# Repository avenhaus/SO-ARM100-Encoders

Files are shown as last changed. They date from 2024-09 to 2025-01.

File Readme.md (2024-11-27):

# <center>Magnetic Encoder Dummy Servo</center>

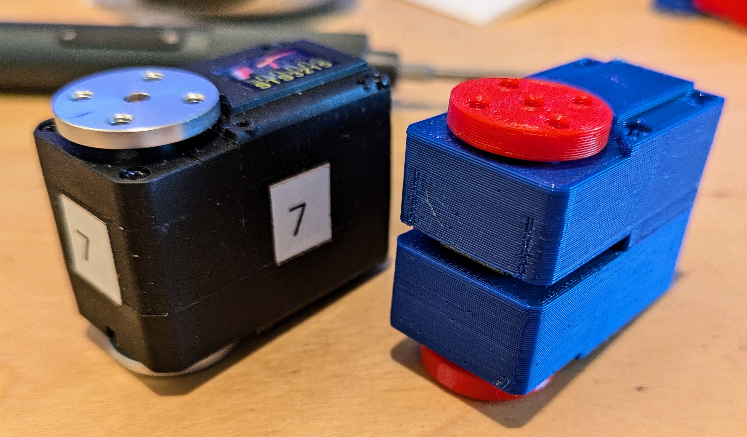
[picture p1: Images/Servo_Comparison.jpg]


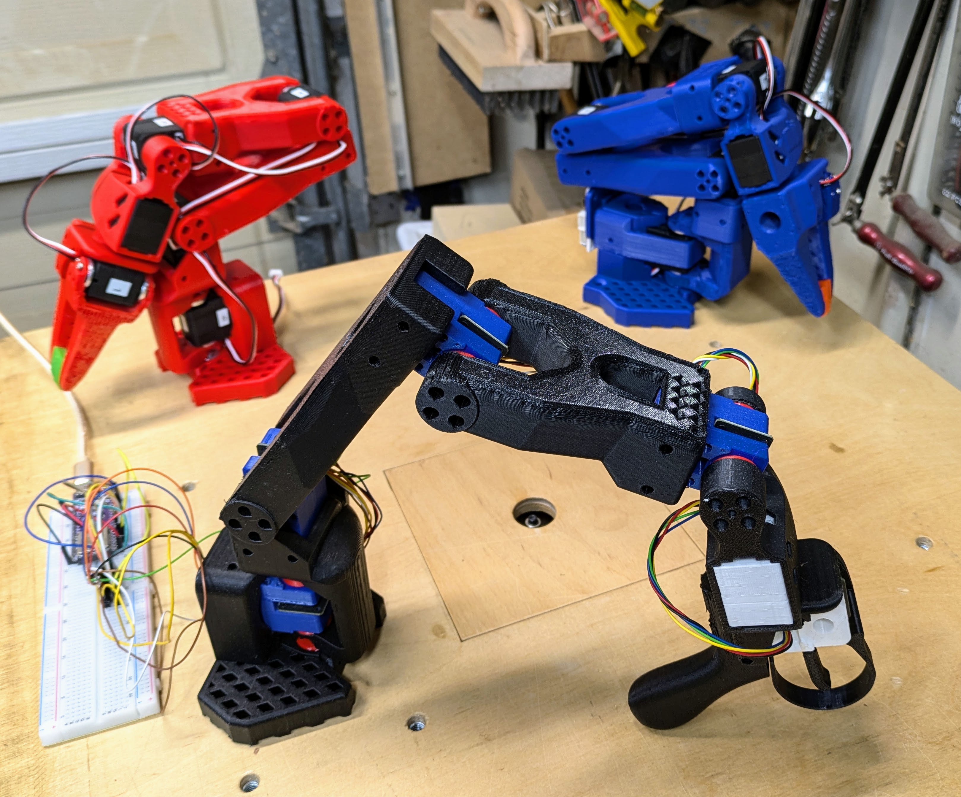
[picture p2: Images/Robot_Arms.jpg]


## Summary
This project is related to 
https://github.com/huggingface/lerobot
and
https://github.com/TheRobotStudio/SO-ARM100

It explores to use much cheaper magnetic encoders for the Leader Arm instead of the regular servos. These dummy servos are also much easier to move manually, as there is no gear train that needs to back drive the servo motor. This makes them ideal for the Leader Arm.

## Custom PCB

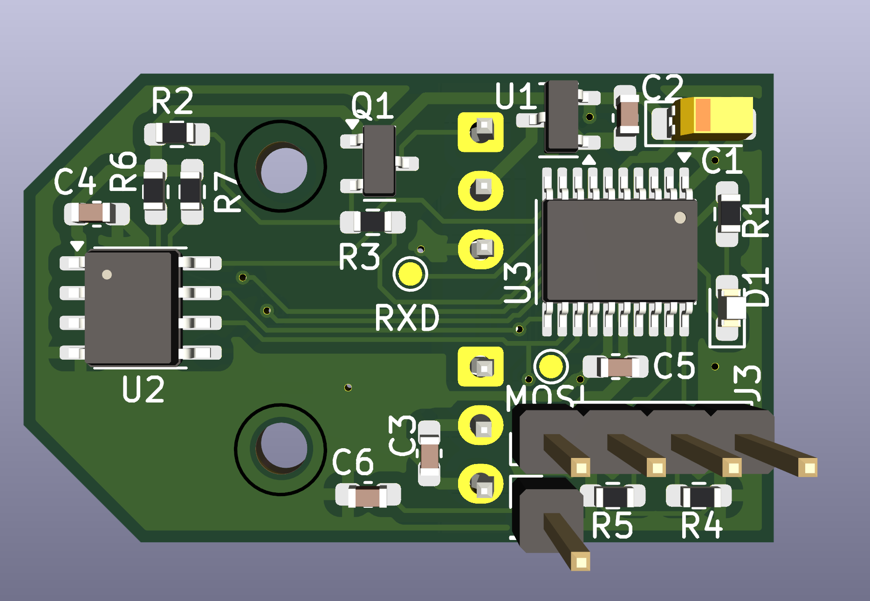
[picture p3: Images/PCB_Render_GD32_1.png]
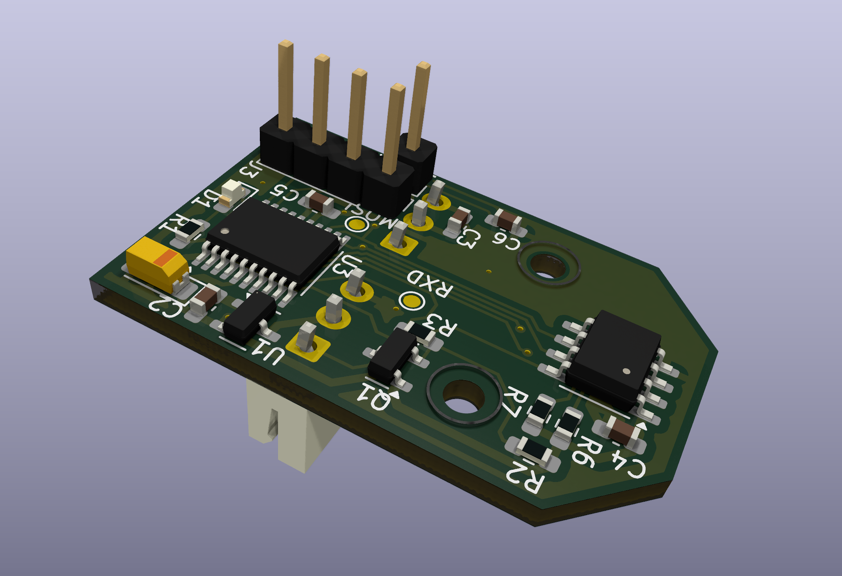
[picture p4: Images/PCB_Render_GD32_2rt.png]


The custom PCB makes it possible to daisy chain magnetic encoders for much easier wiring. The PCB uses a microcontroller that emulates a FeeTech servo. The dummy servos can be connected to the same servo controller board and no special software is needed.

### Manufacturing
TODO: JLCPCB

### Cables and Connectors

FeeTech servos use 3-pin 5264 connectors. However, JST XH connectors are more common and pre-made cables are much easier to find. The PCB can be populated with either of the connector types. If JST connectors are used, an adapter needs to be made to connect to the 5264 connector on the controller board. Alternatively one can simply cut off one end from a pre-made cable and solder it directly to the controller board.

The dummy servos use very little current. So any gauge wire should be ok. However, if they are to be mixed with real servos on the same bus, wire gauge needs to be taken into consideration.

The servos use "reverse double head" cables (pin 1 connected to pin 1, etc.) although in a pinch it's also possible to switch the terminals on "same side' cables yourself.

JST XH: https://www.aliexpress.us/w/wholesale-JST-XH-3.html
JST XH cables: https://www.aliexpress.us/w/wholesale-xh-double-head.html

5264: https://www.aliexpress.us/w/wholesale-5264.html
5264 cables: https://www.aliexpress.us/w/wholesale-5264-double-head.html https://www.aliexpress.us/item/3256806128255434.html

### Magnets

Normally magnetic encoders use special, radially magnetized magnets.

Magnets https://www.aliexpress.us/w/wholesale-encoder-magnets.htm

However, it is also possible to use the regular, axially magnetized 6x3 disk magnets which are cheaper. They just have to be oriented sideways. Print the corresponding servo horn instead. N35 magnets are fine. Nothing fancy is needed.

https://www.amazon.com/s?k=6x3mm+magnet
https://www.aliexpress.us/w/wholesale-6x3-magnet.html

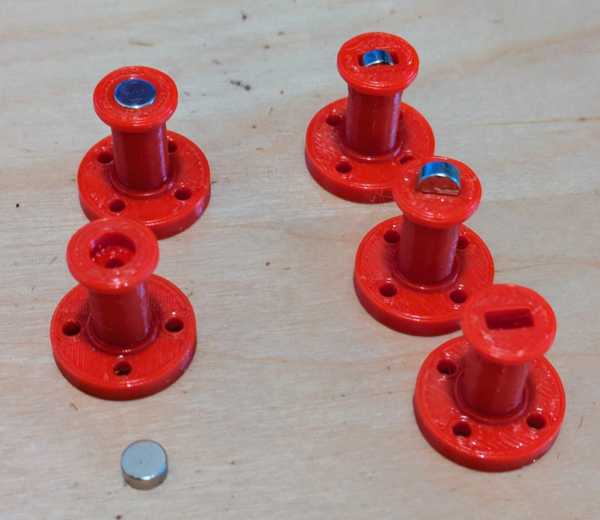
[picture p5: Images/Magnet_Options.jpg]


### Firmware Programming

See: [Firmware](Firmware)

### 3D Printed Servo Housing

<p align="center">
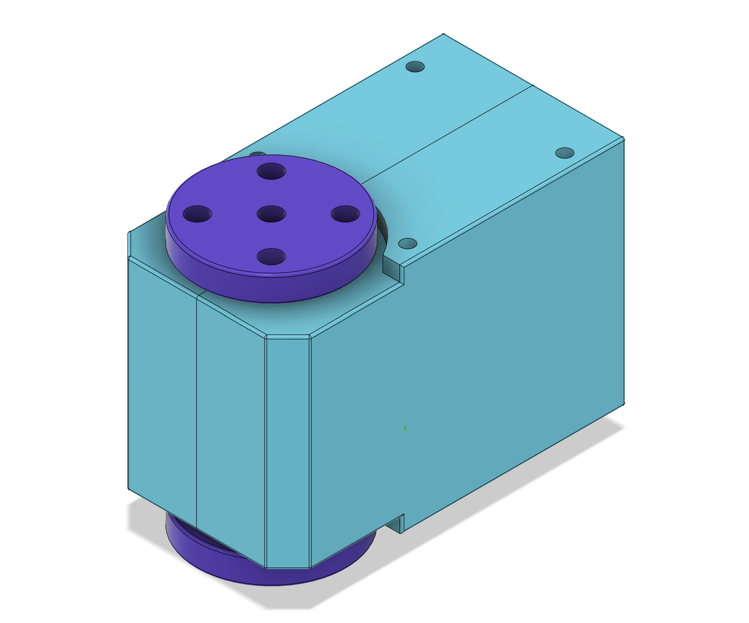
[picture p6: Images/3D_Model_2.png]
 
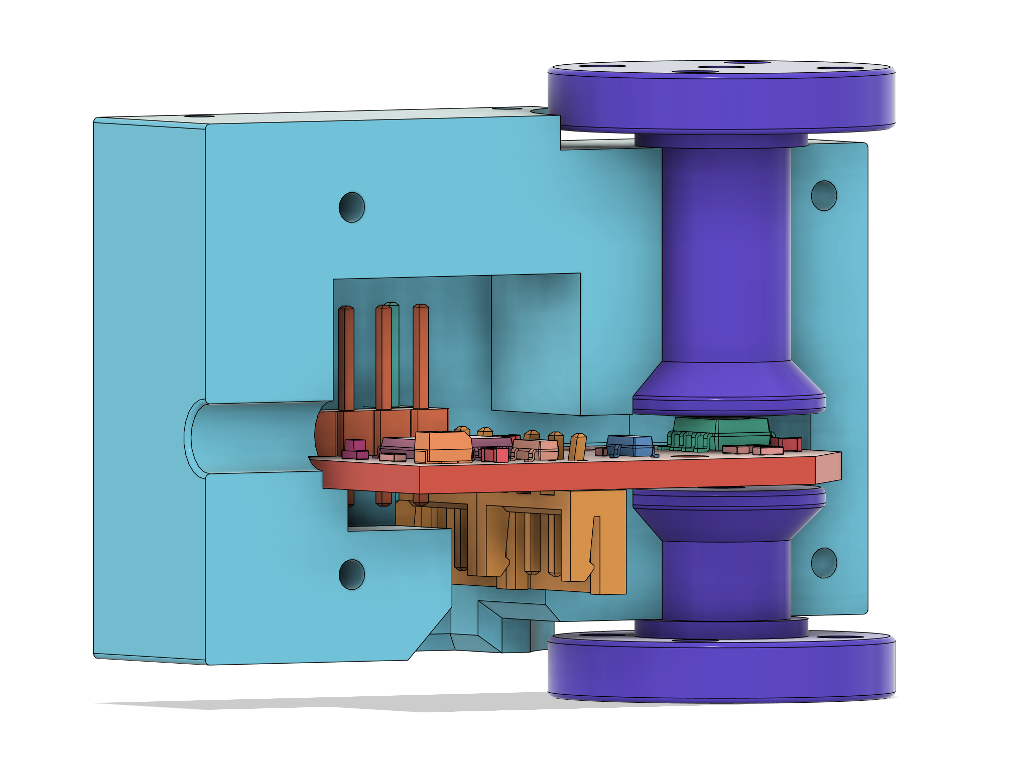
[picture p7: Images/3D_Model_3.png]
</p>
<p align="center">
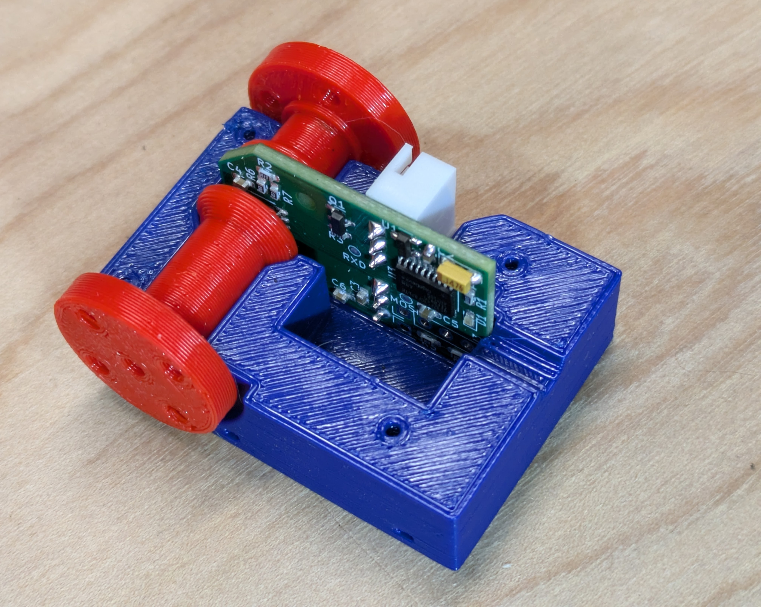
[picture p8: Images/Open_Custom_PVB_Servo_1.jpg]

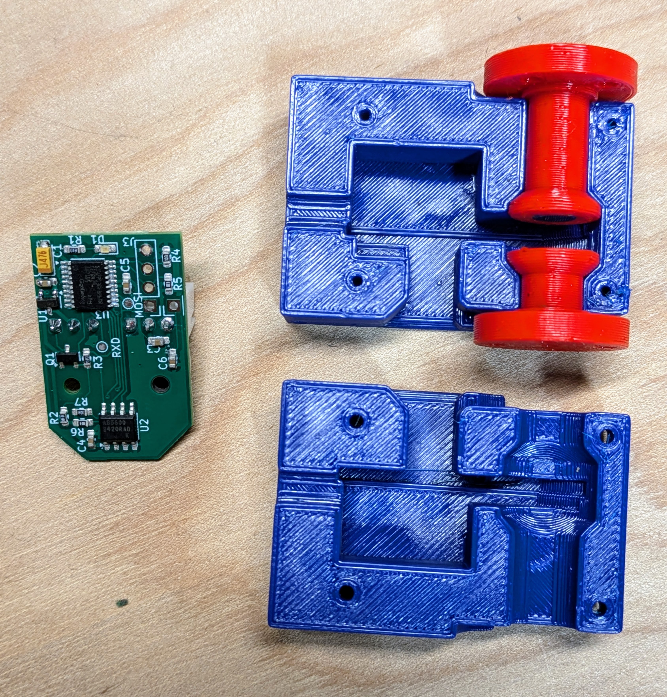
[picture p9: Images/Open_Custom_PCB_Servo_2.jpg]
</p>

## Off the Shelve Hardware

Instead of using a custom PCB it is also possible to use off the shelve parts. This requires more hand wiring.

### Magnetic Rotary Encoders
Currently there are two cheap and popular magnetic encoders on AliExpress, the AS5600 and the MT6701.
The AS5600 is older, has 12 bit resolution (4096) and supports only I2C. Since the chip has only one hard coded ID, that makes it hard to use when multiple of them are needed.
The MT6701 has 14 bit resolution (16,383) and also supports a SSI interface, which is similar to SPI.

AliExpress offers several MT6701 breakout boards some of which can be purchased in low quantities for less than $2 including magnet.

[AliExp MT6701](https://www.aliexpress.com/w/wholesale-MT6701.html)

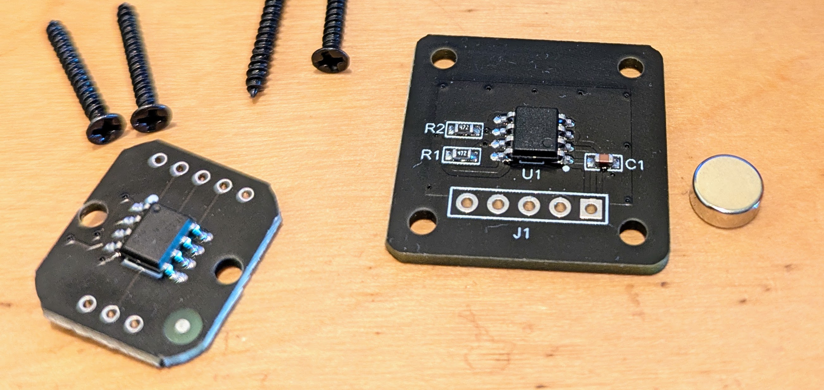
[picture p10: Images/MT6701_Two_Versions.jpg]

<p>






The larger version only has the I2C pins on the header and must be modified to work with SSI. The trace to the middle pin of the header needs to be cut and IC pin 8 lifted and connected to that header pin instead. It is also slightly too large, sticking out a bit in front of the servo. It can be made to work, but the smaller board is much easier to use and therefor recommended. However the smaller board does not come with magnets. They must be purchased separately. Only radially magnetized magnets can be used. Normally disk magnets are magnetized axially. 

[AliExp Radial Magnets](https://www.aliexpress.us/item/3256804628068823.html)

### 3D Printed Servo Housing

There are two slightly different versions of the housing. The simple version does not retain the servo horns by itself. It relies on the structure of the robot arm to keep them in place. This version is slightly simpler and is used for the lower 4 arm servos.

The wrist and gripper need the horn to be held in place by the servo itself. For these joints the top is split into two parts and the horn axle is not just a straight cylinder.

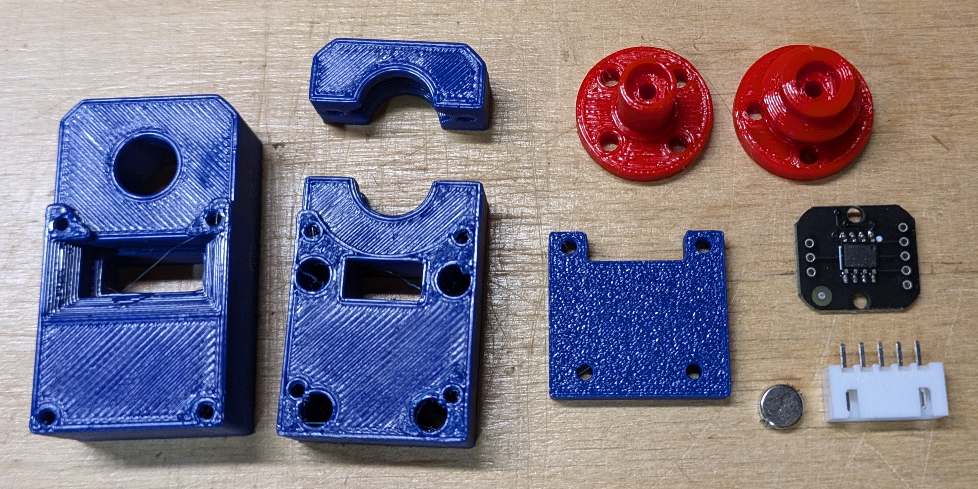
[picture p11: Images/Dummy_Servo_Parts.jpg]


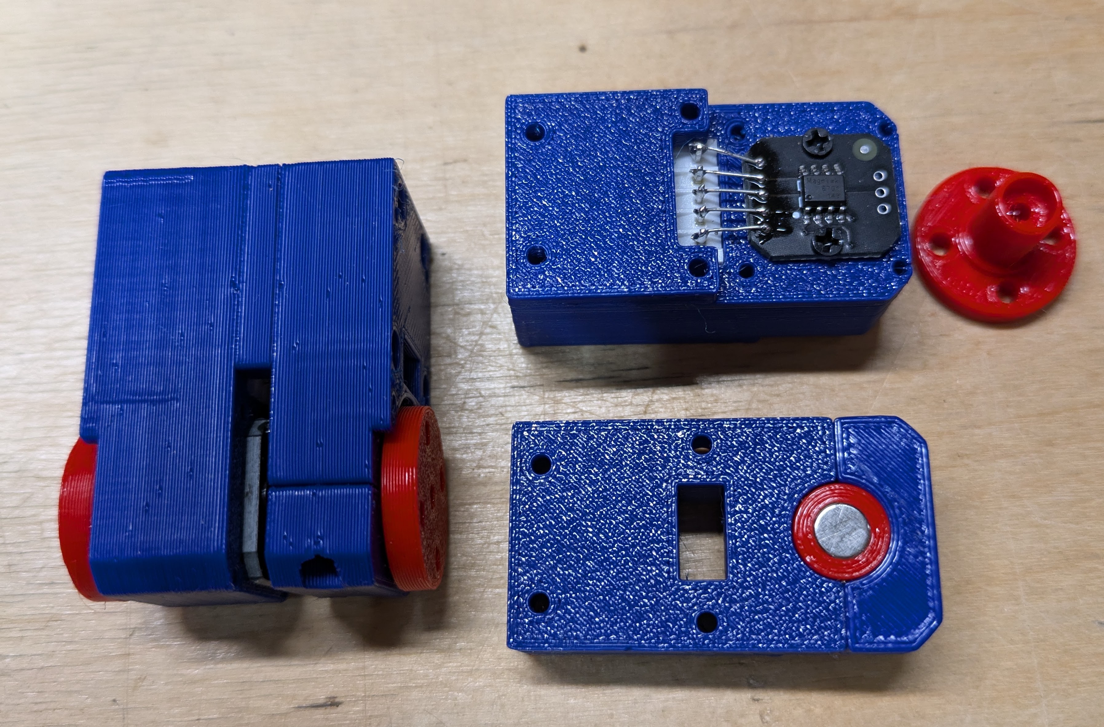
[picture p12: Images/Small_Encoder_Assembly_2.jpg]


**Big Board Alternative**

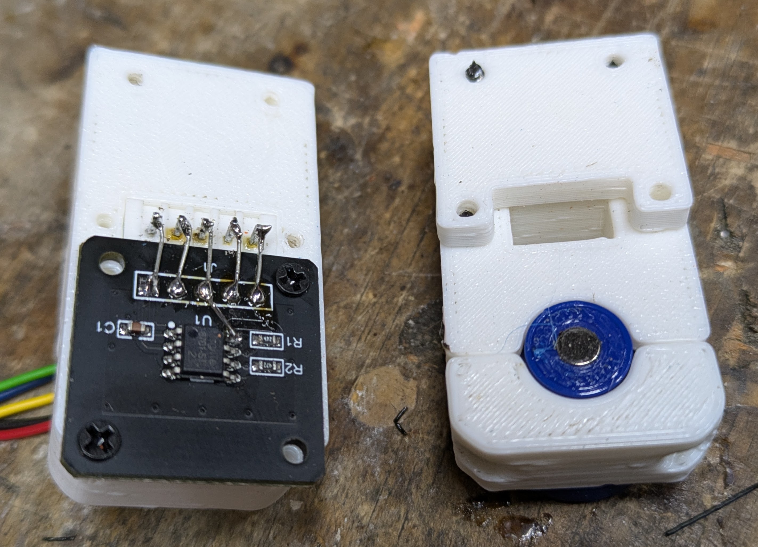
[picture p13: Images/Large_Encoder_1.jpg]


The [Dummy Servo](./Hardware) is 3D printed.
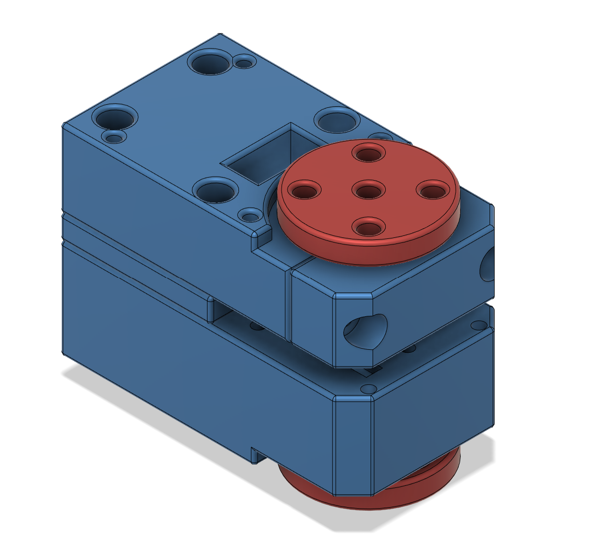
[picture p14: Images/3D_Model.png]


## Software

A simple [Arduino](./Arduino) / PlatformIO project is used to read the six encoders and send their values over a serial USB port to the PC.

On the PC side a small [Python](./Python) program receives the values from the serial port and uses the Feetech-SDK to control the servos of the follower arm.

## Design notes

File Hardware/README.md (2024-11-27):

# <center>3D Models</center>



## Custom PCB

The PCB can be populated with either an AS5600 or an MT6701 encoder. The MCU can automatically figure out which one is connected. However at the moment there are only non blocking drivers for the AS5600.

There are two versions of the PCB. One for the GD32F130 microcontroller, which is also used by Feetech servos. The other one uses a CH32V003 instead, which is cheaper. However no firmware has been written yet for the CH32V003 and the PCB has not been tested.

### Programming Dongles

The GD32F130 is programmed with a ST-LINK V2 dongle: https://www.aliexpress.us/item/3256805941217455.html / https://www.aliexpress.us/item/3256805308308820.html

The CH32V003  is programmed with a WCH-linkE dongle: https://www.aliexpress.us/item/3256804084637506.html

### Solder Stencil

[Cutting solder paste stencils from Mylar YouTube video](https://www.youtube.com/watch?v=mw0mskVCvis)
[make_stencil.py GitHub](https://github.com/bminch/Eclectronics)

- Open KicCAD PCB => Plot 
- Select layers: F. Paste and Edge Cuts
- Plot Format: SVG
- python make_stencil.py gd32_encoder

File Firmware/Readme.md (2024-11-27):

# <center>Magnetic Encoder Dummy Servo Firmware</center>

The firmware implements the Dynamixel protocol to emulate a FeeTech servo. It reads the magnetic encoder and also supports writing configurations to EEPROM.

The firmware is developed in Visual Studio Code with the PlatformIO extension. The firmware is based on the Arduino framework.

### Drivers

Arduino drivers are blocking. They contain busy loops that wait while the sensor is being read. The Dynamixel protocol which is used to control the FeeTech servos times out if there is no immediate response upon a communication request. For this reason custom, non blocking drivers for the I2C / SPI peripherals as well as the magnetic encoders have to be implemented.

## Programming

The GD32F130 is programmed with a ST-LINK V2 dongle: https://www.aliexpress.us/item/3256805941217455.html / https://www.aliexpress.us/item/3256805308308820.html

The CH32V003  is programmed with a WCH-linkE dongle: https://www.aliexpress.us/item/3256804084637506.html

The PCB has holes for a programming header, but that does not need to be populated. It is usually possible to just loosely insert the connectors and press them sideways with a finger while programming to make good enough contact.

**The programming header has a 3.3V pin. That 3.3V should only be connected if there is no voltage on the servo com headers!**

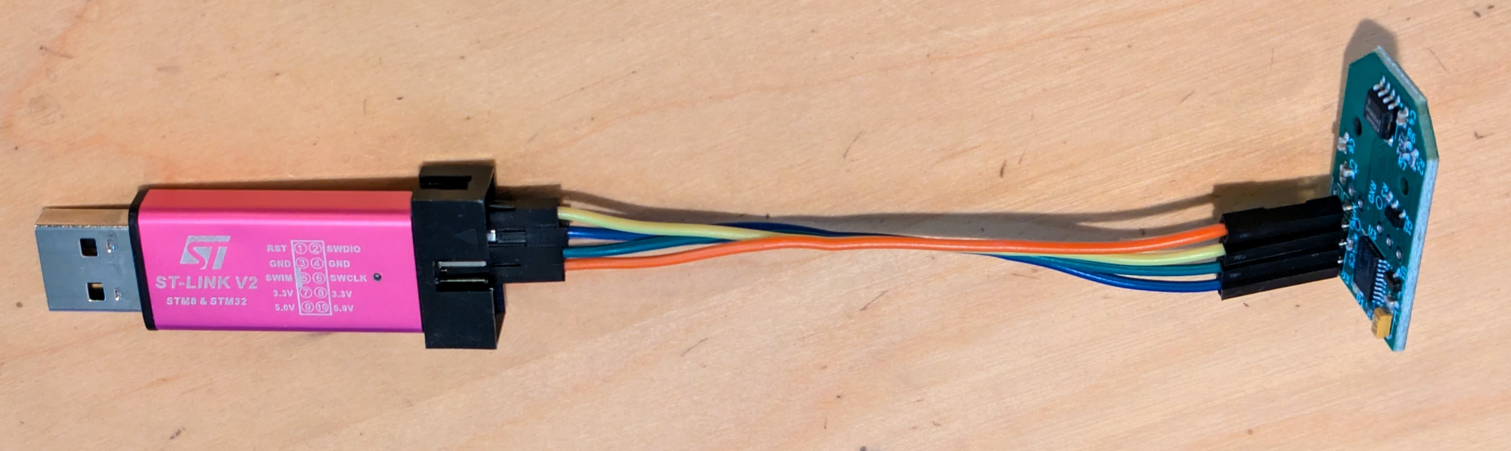
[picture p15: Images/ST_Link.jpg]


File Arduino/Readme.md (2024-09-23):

# Controller to read MT6701 magnetic encoders

PlatformIO / Arduino code to read six MT6701 magnetic encoders over SSI (SPI) and send the data to the UART serial port.

The MT6701 has a 14 bit resolution (0-16383).
To address six encoders, 10 wires are needed: VCC, GND, Clock, Data, 6 x CS.

https://www.lcsc.com/datasheet/lcsc_datasheet_2110291630_Magn-Tek-MT6701QT-STD_C2913974.pdf

## Output Format

The output are comma separated values. The first value is the timestamp in ms since the controller reset. This is followed by angle (float) and status (int) pairs for each encoder.

Lines that start with # are text status messages.

## Calibration

Move all arm joints to the home postion and press the button on the dev board.
This will save the current positions to EEPROM. 
All angles from now on will be sent as realtive to this position.

## Connections

* SPI_SCK_PIN 12
* SPI_MISO_PIN 13
* SPI_CS0_PIN 4
* SPI_CS1_PIN 5
* SPI_CS2_PIN 6
* SPI_CS3_PIN 7
* SPI_CS4_PIN 8
* SPI_CS5_PIN 9

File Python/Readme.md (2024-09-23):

# Simple Follower

Read the MT6701 magnetic encoders and send values to the Feetech STS3215 servos of a follower arm.

conda create -y -n encoder_arm python=3.10
conda activate encoder_arm
pip install feetech-servo-sdk

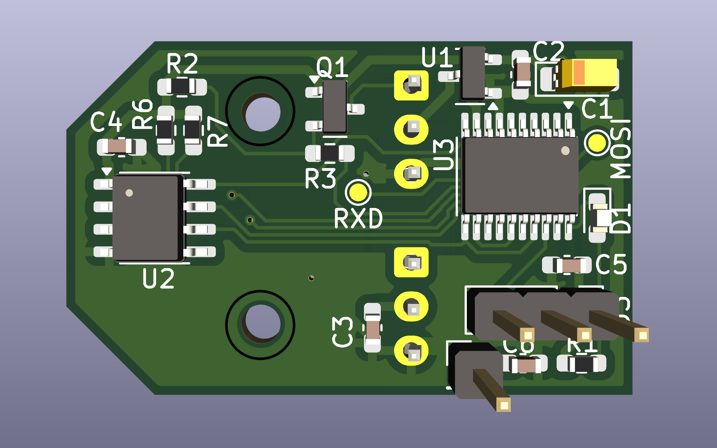
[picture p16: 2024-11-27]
Images/PCB_Render_CH32_1.png

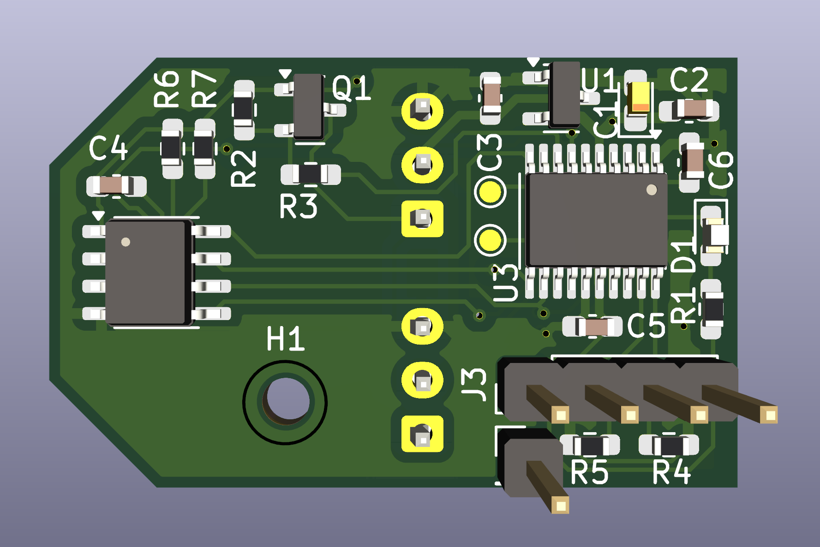
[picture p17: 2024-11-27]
Images/PCB_Render_1.png

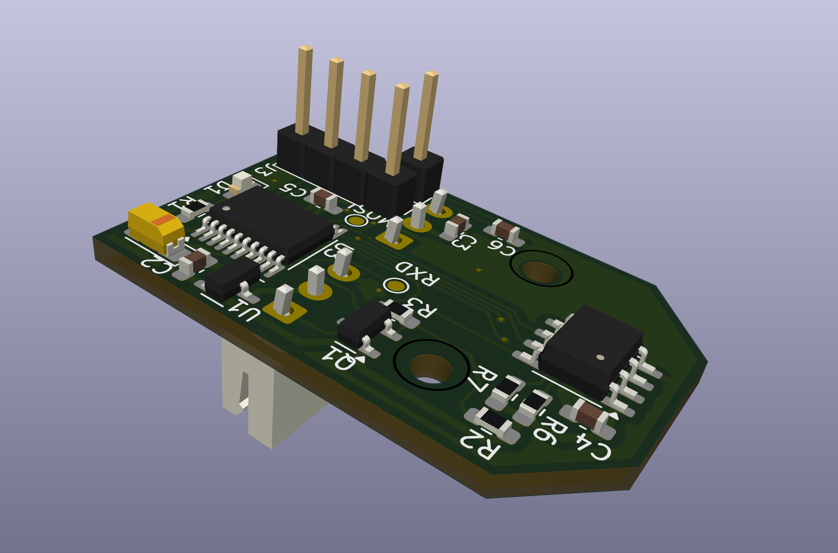
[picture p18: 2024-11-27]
Images/PCB_Render_GD32_2.png

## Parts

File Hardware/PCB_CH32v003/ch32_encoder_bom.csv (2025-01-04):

Id | Designator | Footprint | Quantity | Designation | Supplier and ref
1 | MOSI | TestPoint_Pad_D1.0mm | 1 | MOSI
2 | TP1 | PinHeader_1x01_P2.54mm_Vertical | 1 | RST
3 | C1 | CP_EIA-3216-18_Kemet-A_Pad1.58x1.35mm_HandSolder | 1 | 47uF
4 | C2,C5,C3,C6,C4 | C_0603_1608Metric_Pad1.08x0.95mm_HandSolder | 5 | 100nF
5 | R1 | R_0603_1608Metric_Pad0.98x0.95mm_HandSolder | 2 | 1K
6 | J3 | PinHeader_1x03_P2.54mm_Vertical | 1 | Conn_01x03_Pin
7 | U2 | SO-8_3.9x4.9mm_P1.27mm | 1 | AS5600 or MT6701CT
8 | R3 | R_0603_1608Metric_Pad0.98x0.95mm_HandSolder | 1 | 100
9 | R2,R7,R6 | R_0603_1608Metric_Pad0.98x0.95mm_HandSolder | 2 | 10K
10 | D1 | LED_0603_1608Metric_Pad1.05x0.95mm_HandSolder | 1 | LED
11 | U1 | SOT-23-3 | 1 | HT7533S
12 | RXD | TestPoint_Pad_D1.0mm | 1 | RXD
13 | Q1 | SOT-23 | 1 | 2N7002K
14 | U3 | TSSOP-20_4.4x6.5mm_P0.65mm | 1 | CH32V003FxPx
15 | J1,J2 | JST_1x03_P2.50mm_Vertical | 2 | Conn_01x03_Pin

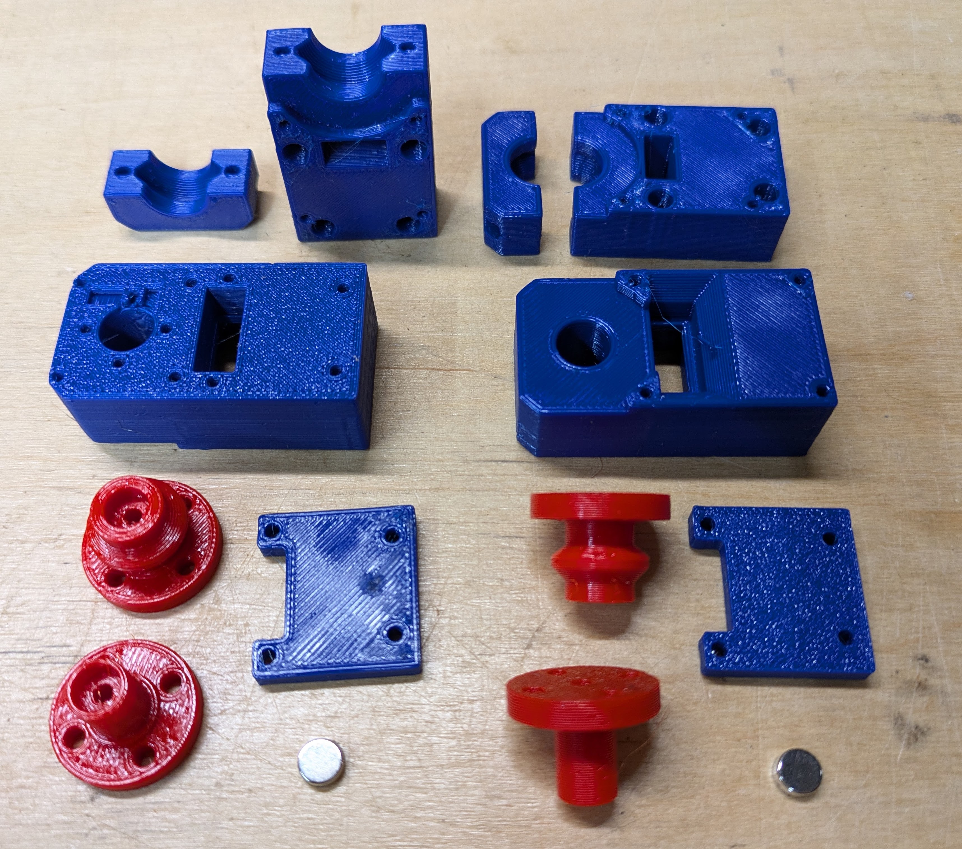
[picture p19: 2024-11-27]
Images/3D_Printed_Parts.jpg

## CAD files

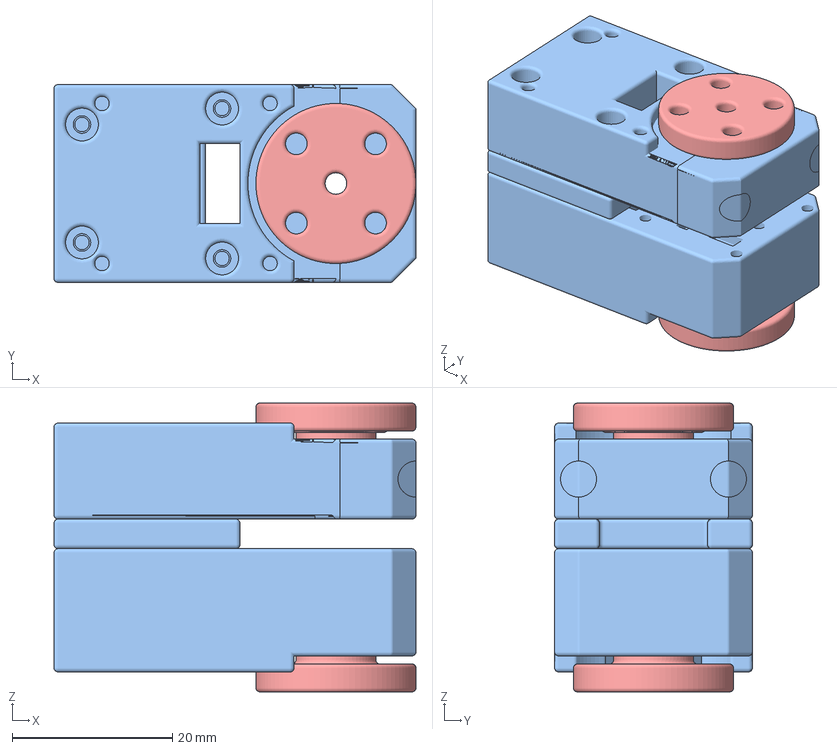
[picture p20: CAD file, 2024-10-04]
Hardware/3D_Models/Off the shelve PCB/Encoder Dummy Servo.3mf
45.2 x 24.7 x 36.1 mm
Clip
Horn x 3
Top

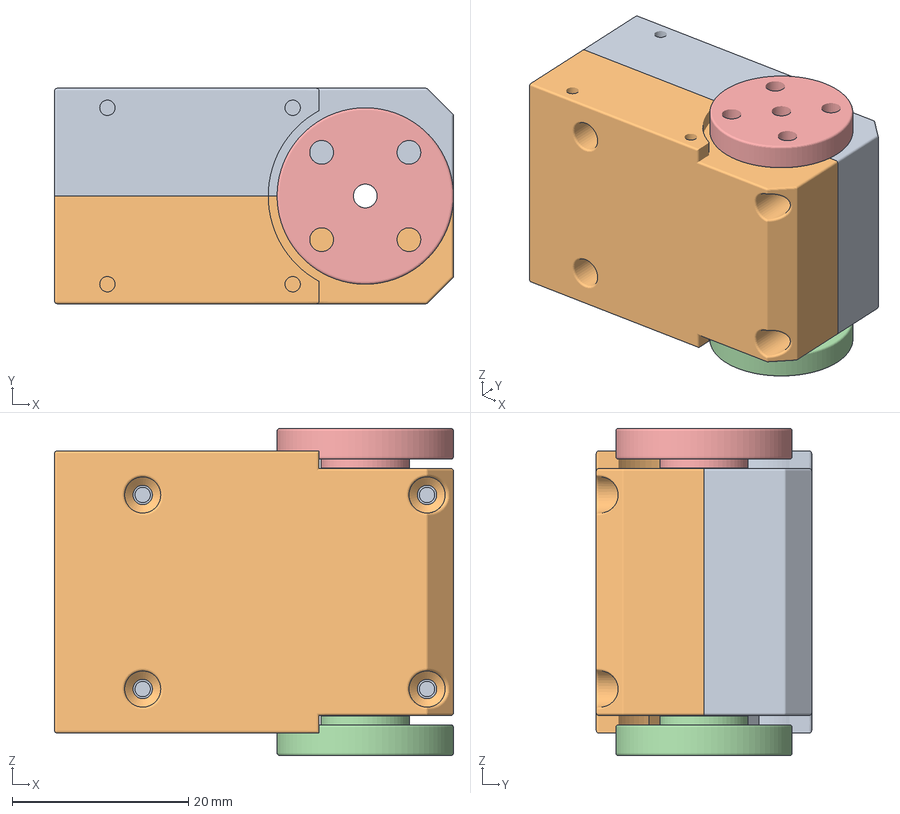
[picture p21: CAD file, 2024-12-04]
Hardware/3D_Models/Servo Custom PCB V2/Servo Custom PCB V2.3mf
45.2 x 24.4 x 37.1 mm
Back
Front
Horn Magnet 6x3
Idle Horn
Magnet Horn 5mm radial
Magnet Horn 6mm radial

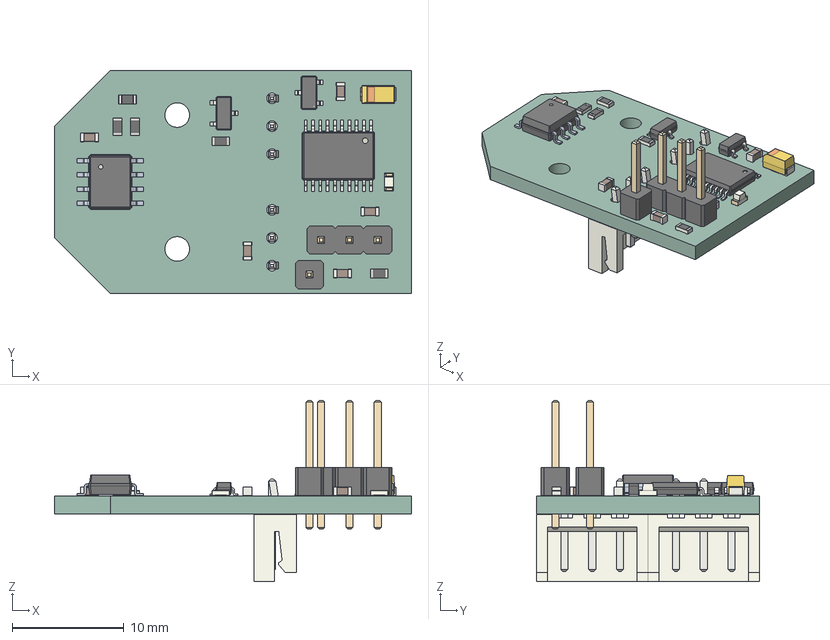
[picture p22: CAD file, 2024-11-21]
Hardware/PCB_CH32v003/ch32_encoder_v0.7.step
32.0 x 20.0 x 16.2 mm
PinHeader_1x01_P254mm_Vertical
CP_EIA_3216_18_Kemet_A
C_0603_1608Metric x 5
R_0603_1608Metric x 5
PinHeader_1x03_P254mm_Vertical
CQ assembly
LED_0603_1608Metric
SOT-23-3
SOT_23
TSSOP_20_44x65mm_P065mm
JST_B3B_EH_A x 2
ch32_encoder_PCB

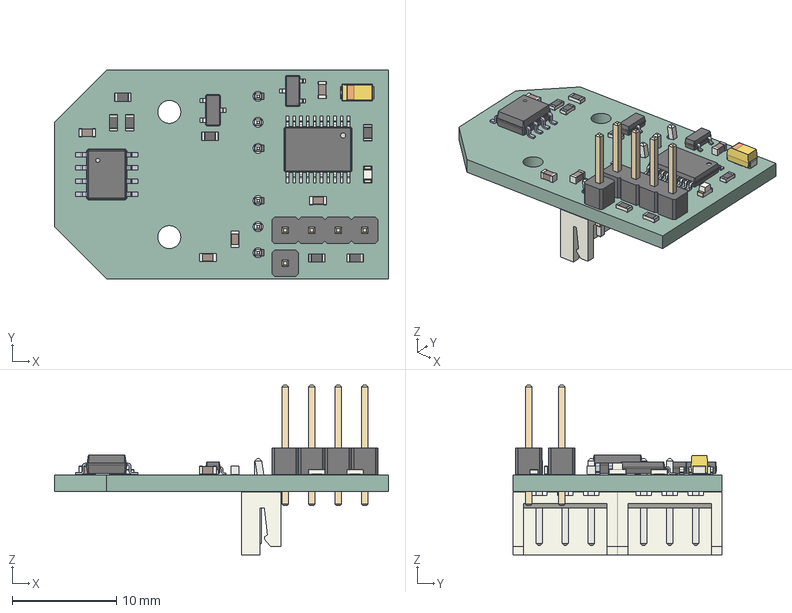
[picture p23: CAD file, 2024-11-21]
Hardware/PCB_GD32F130/gd32_encoder_v0.7.step
32.0 x 20.0 x 16.2 mm
R_0603_1608Metric x 7
PinHeader_1x01_P254mm_Vertical
CP_EIA_3216_18_Kemet_A
C_0603_1608Metric x 5
TSSOP_20_44x65mm_P065mm
CQ assembly
PinHeader_1x04_P254mm_Vertical
LED_0603_1608Metric
SOT-23-3
SOT_23
JST_B3B_EH_A x 2
gd32_encoder_PCB

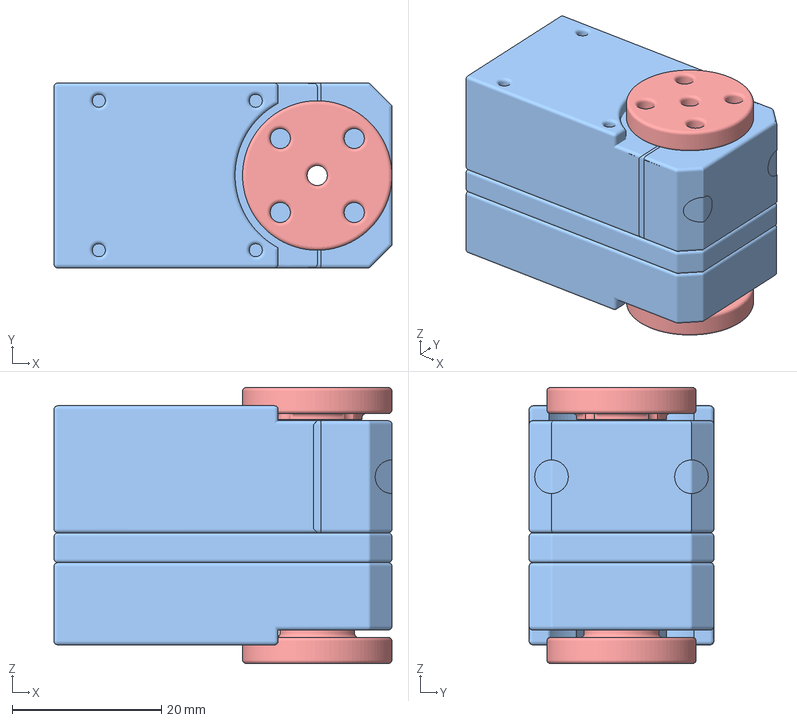
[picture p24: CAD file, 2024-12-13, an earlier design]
Hardware/3D_Models/Servo Custom PCB V1/Servo Custom PCB V1.3mf
45.2 x 24.7 x 37.0 mm
Clip
Horn x 3
Top

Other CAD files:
Hardware/3D_Models/Off the shelve PCB/Encoder Dummy Servo.f3d
Hardware/3D_Models/Servo Custom PCB V1/Servo Custom PCB V1.f3d
Hardware/3D_Models/Servo Custom PCB V2/Servo Custom PCB V2.f3d

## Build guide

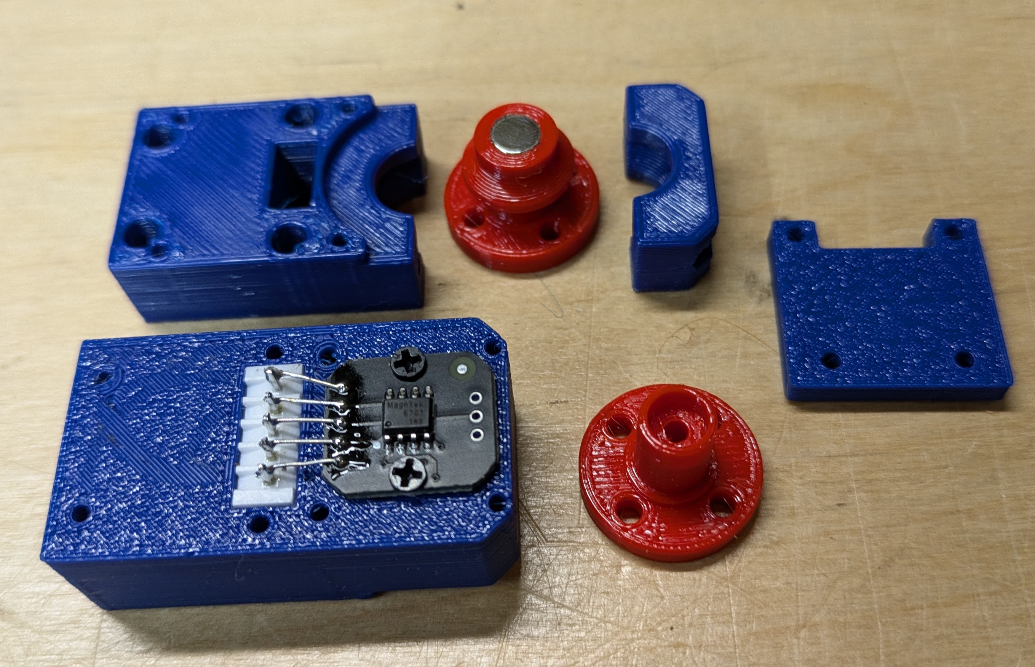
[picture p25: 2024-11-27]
Images/Small_Encoder_Assembly_1.jpg

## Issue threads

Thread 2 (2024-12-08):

Pre-assembled or Custom PCB: Which Do You Recommend?

seanwhen, 2024-12-08:
I’m not very experienced with PCB design, and in the past, my soldering attempts often resulted in damaged or burned boards. For the MT6701, do I need to purchase an ESP32 to use the pre-assembled board? I didn’t see this combination explicitly mentioned in the project’s BOM. From the images, it seems that the encoder is fixed onto a 3D-printed mount, with all the wires connected to a breadboard, which then interfaces with an ESP32/STM32. Is this understanding correct?

Additionally, in the video you shared earlier, the delay seemed comparable to the STS3215 servo. Among the three options—pre-assembled MT6701, custom PCB, and the STS3215 servo—how do they compare in terms of precision based on your experience? Do you see significant advantages in moving towards custom PCBs, or would you recommend sticking with the off-the-shelf solutions? Thank you for your insights!

avenhaus, 2024-12-11:
Hi Seanwen, the custom boards are SMD and probably not easy to assemble yourself if you don't already have experience. JLCPCB can assemble boards for you, but I have not tried this myself and don't know what it would cost.

For pre assembled boards yes, you will also need to buy an ESP32 board, which will drive the individual sensor boards and translate the data to serial data and connect to the PC. Delay should not be an issue and MT6701 actually have higher resolution than the STS3125.

However be aware that there is not the same software support on the PC side. I have a simple program to do remote control of another arm, but I have not looked into how to integrate this into the other SO-ARM100 software to do training etc. So there is still a driver portion missing.

seanwhen, 2024-12-12:
Hi, thank you for your detailed response! I’ve completed the custom PCB design and 3D enclosure based on your project and am about to assemble and test the PCB. From your explanation, it seems that the basic control program for the custom PCB works with “飞特.exe,” but integrating it seamlessly into LeRobot might pose some challenges. Is this correct?

Additionally, from my understanding, the custom PCB design already includes a chip on each board, so it does not require an ESP32, whereas the MT6701-based solution does require an ESP32. Is that correct? Based on this, I’d like to clarify the following points:
	1.	Using custom PCBs with LeRobot:
If I use the custom PCB (with a chip on each board), will I still need to write additional drivers to make it compatible with LeRobot?
Does LeRobot currently support extending to use custom PCBs directly, or would I need to modify its source code?
	2.	Future plans for control program updates:
Do you plan to update the control program to integrate custom PCB support into LeRobot?
Alternatively, could you share the protocol details or source code of the existing control program so I can build on it for further development and integration?

Thank you again for your amazing work, and I look forward to your reply!

avenhaus, 2024-12-13:
Oh wow, you are brave! Good luck with the assembly!

Yes, if you use the custom PCB, you do not need an ESP32. The idea is that the custom PCB will emulate an STS3215 and look the same to the software. Instead you will need the driver board from FeeTech or WaveShare to connect to the PC, same as servos.

1) In the end LeRobot should not be able to tell the difference between an STS3215 and these boards. So no custom drivers are needed. But [iamliustar](https://github.com/iamliustar) found a few things missing in the current firmware that need to be added. Please see https://github.com/avenhaus/SO-ARM100-Encoders/issues/1 for details.

2) No changes should be needed in LeRobot unless you use the ESP32 with of the shelve encoders. The FeeTech servos and custom PCBs use Dynamixel Protocol V1

https://emanual.robotis.com/docs/en/dxl/protocol1/
https://www.theremino.com/wp-content/uploads/files/SmartMotors/Feetech_Motors_Programming_ENG.pdf

seanwhen, 2024-12-16:
Hi, I finished soldering all the boards today. When I tried running `/Firmware/SO-Encoder100` directly in PlatformIO, the compilation went fine, but when uploading to the PCB, I encountered this error. I tested all the boards, and the same issue occurred every time. Do you know what might be causing this?

Here’s the error log:

```
Configuring upload protocol...
AVAILABLE: blackmagic, cmsis-dap, gdlinkcli, jlink, serial, sipeed-rv-debugger, stlink
CURRENT: upload_protocol = stlink
Uploading .pio/build/genericGD32F130F8/firmware.elf
xPack OpenOCD x86_64 Open On-Chip Debugger 0.11.0+dev (2021-12-07-19:33)
Licensed under GNU GPL v2
For bug reports, read
        http://openocd.org/doc/doxygen/bugs.html
debug_level: 1

hla_swd
0
Error: open failed
in procedure 'program'
** OpenOCD init failed **
shutdown command invoked

*** [upload] Error 1
=================================== [FAILED] Took 18.73 seconds ===================================

Environment        Status    Duration
-----------------  --------  ------------
genericGD32F130F8  FAILED    00:00:18.728
============================== 1 failed, 0 succeeded in 00:00:18.728 ==============================
```

seanwhen, 2025-01-25:
Hey guy, I tried to identify the issue. After flashing the firmware and powering on, the red light flashes briefly, but I couldn’t find the motor in Feetech. I used a 12.6V power supply for the driver board, but the 3216 47uF capacitor on C1 was originally purchased with a 6.3V rating. Could this be related? I just purchased a 16V 47uF capacitor and am unsure if it will resolve the issue. I’m using the F8 chip and didn’t modify anything in the SDK, directly flashing your latest firmware Firmware/SO-Encoder100. Do you know why the motor cannot be detected? The communication is set to 115200.

seanwhen, 2025-01-26:
This is the result of my burn, I am not very skilled in embedded programming, firmware burn 'is your latest update.

Verbose mode can be enabled via `-v, --verbose` option
CONFIGURATION: https://docs.platformio.org/page/boards/gd32/genericGD32F130F8.html
PLATFORM: GD GD32 (1.0.0+sha.646efb5) > GD32F130F8 (8k RAM, 64k Flash)
HARDWARE: GD32F130F8P6 48MHz, 8KB RAM, 64KB Flash
DEBUG: Current (stlink) External (blackmagic, cmsis-dap, jlink, sipeed-rv-debugger, stlink)
PACKAGES:
 - framework-arduinogd32 @ 4.20000.210603+sha.4c9e33f
 - tool-dfuutil @ 1.9.211020
 - tool-gdlinkcli @ 2.40611.220807+sha.cddd14e
 - tool-openocd-gd32 @ 2.1100.211207 (11.0)
 - tool-stm32duino @ 1.0.1
 - toolchain-gccarmnoneeabi @ 1.90201.191206 (9.2.1)
LDF: Library Dependency Finder -> https://bit.ly/configure-pio-ldf
LDF Modes: Finder ~ deep, Compatibility ~ soft
Found 12 compatible libraries
Scanning dependencies...
Dependency Graph
|-- EEPROM @ 0.1.0
|-- FlashStorage @ 0.1.0
|-- Wire @ 1.0
Building in release mode
Checking size .pio/build/genericGD32F130F8/firmware.elf
Advanced Memory Usage is available via "PlatformIO Home > Project Inspect"
RAM:   [========= ]  86.5% (used 7084 bytes from 8192 bytes)
Flash: [=         ]  14.3% (used 9344 bytes from 65536 bytes)
Configuring upload protocol...
AVAILABLE: blackmagic, cmsis-dap, gdlinkcli, jlink, serial, sipeed-rv-debugger, stlink
CURRENT: upload_protocol = stlink
Uploading .pio/build/genericGD32F130F8/firmware.elf
xPack OpenOCD x86_64 Open On-Chip Debugger 0.11.0+dev (2021-12-07-19:33)
Licensed under GNU GPL v2
For bug reports, read
        http://openocd.org/doc/doxygen/bugs.html
debug_level: 1

hla_swd
0
target halted due to debug-request, current mode: Thread
xPSR: 0x01000000 pc: 0x08001a20 msp: 0x20002000
** Programming Started **
** Programming Finished **
** Verify Started **
** Verified OK **
** Resetting Target **
shutdown command invoked
================================================ [SUCCESS] Took 2.03 seconds ================================================

Environment        Status    Duration
-----------------  --------  ------------
genericGD32F130F8  SUCCESS   00:00:02.033

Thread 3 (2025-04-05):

Problems encountered while using the MT6701 encoder

CWEIB, 2025-04-05:
Hello, after I replicated the setup, it seems that the MT6701 wasn't properly detected via I2C. When I uncommented the related MT6701 code, it was able to read data normally, but I'm not sure how to make it work correctly. The values being read also seem to have some deviation.
What steps should I take to properly use the MT6701 encoder?

Closed 2025-04-05.

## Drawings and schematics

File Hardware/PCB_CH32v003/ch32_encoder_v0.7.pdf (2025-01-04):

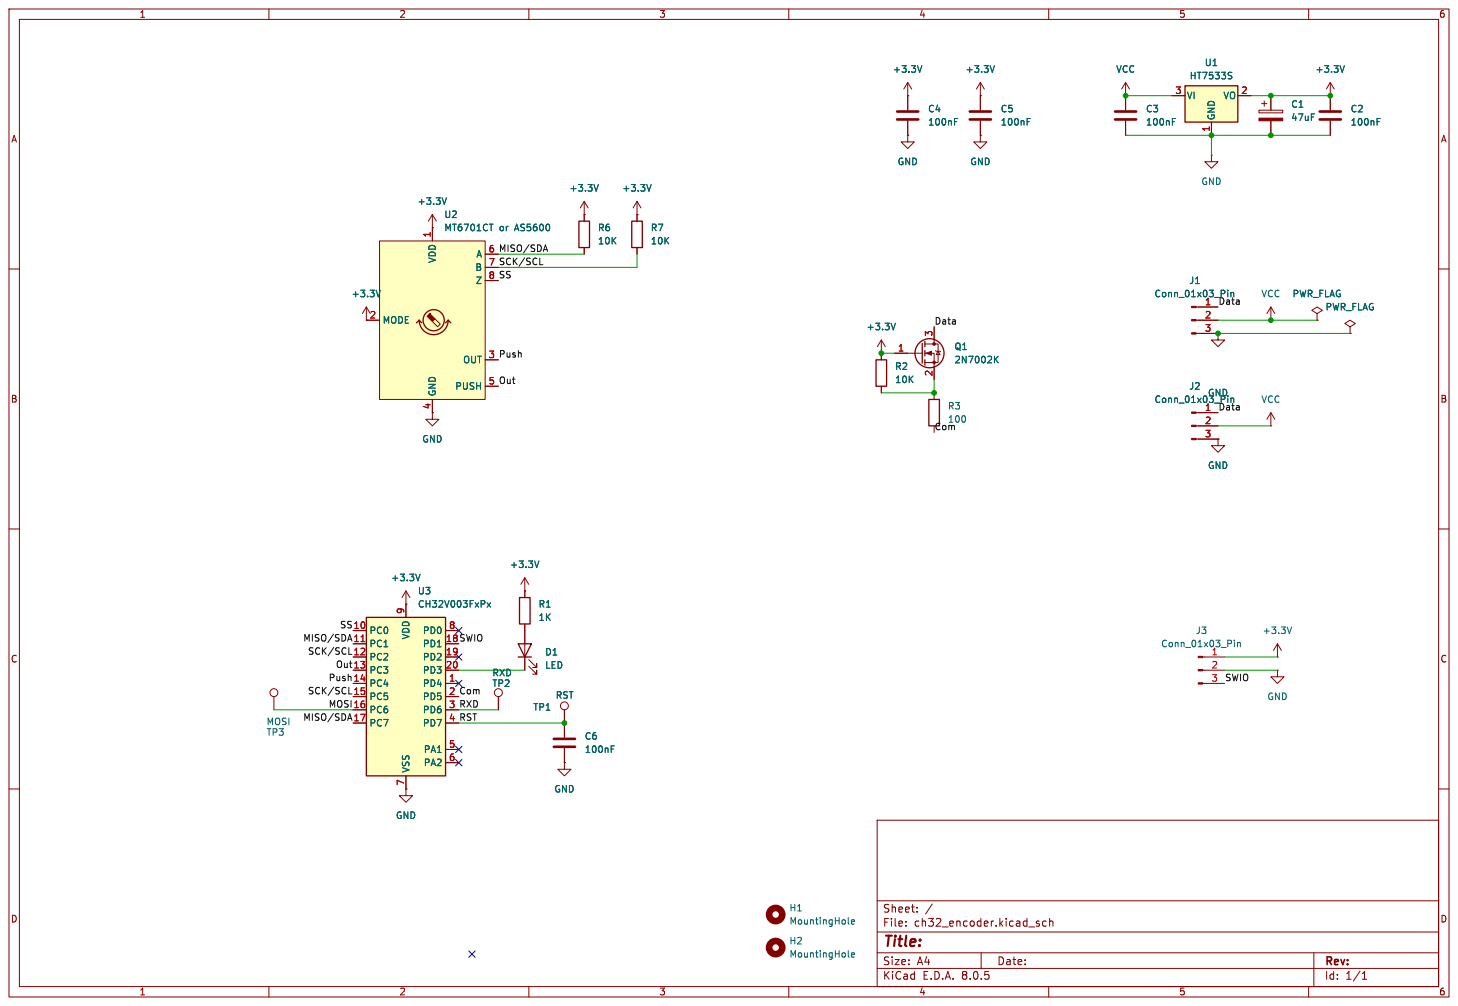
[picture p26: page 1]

Id: 1/1 Title: File: ch32_encoder.kicad_sch Sheet: /

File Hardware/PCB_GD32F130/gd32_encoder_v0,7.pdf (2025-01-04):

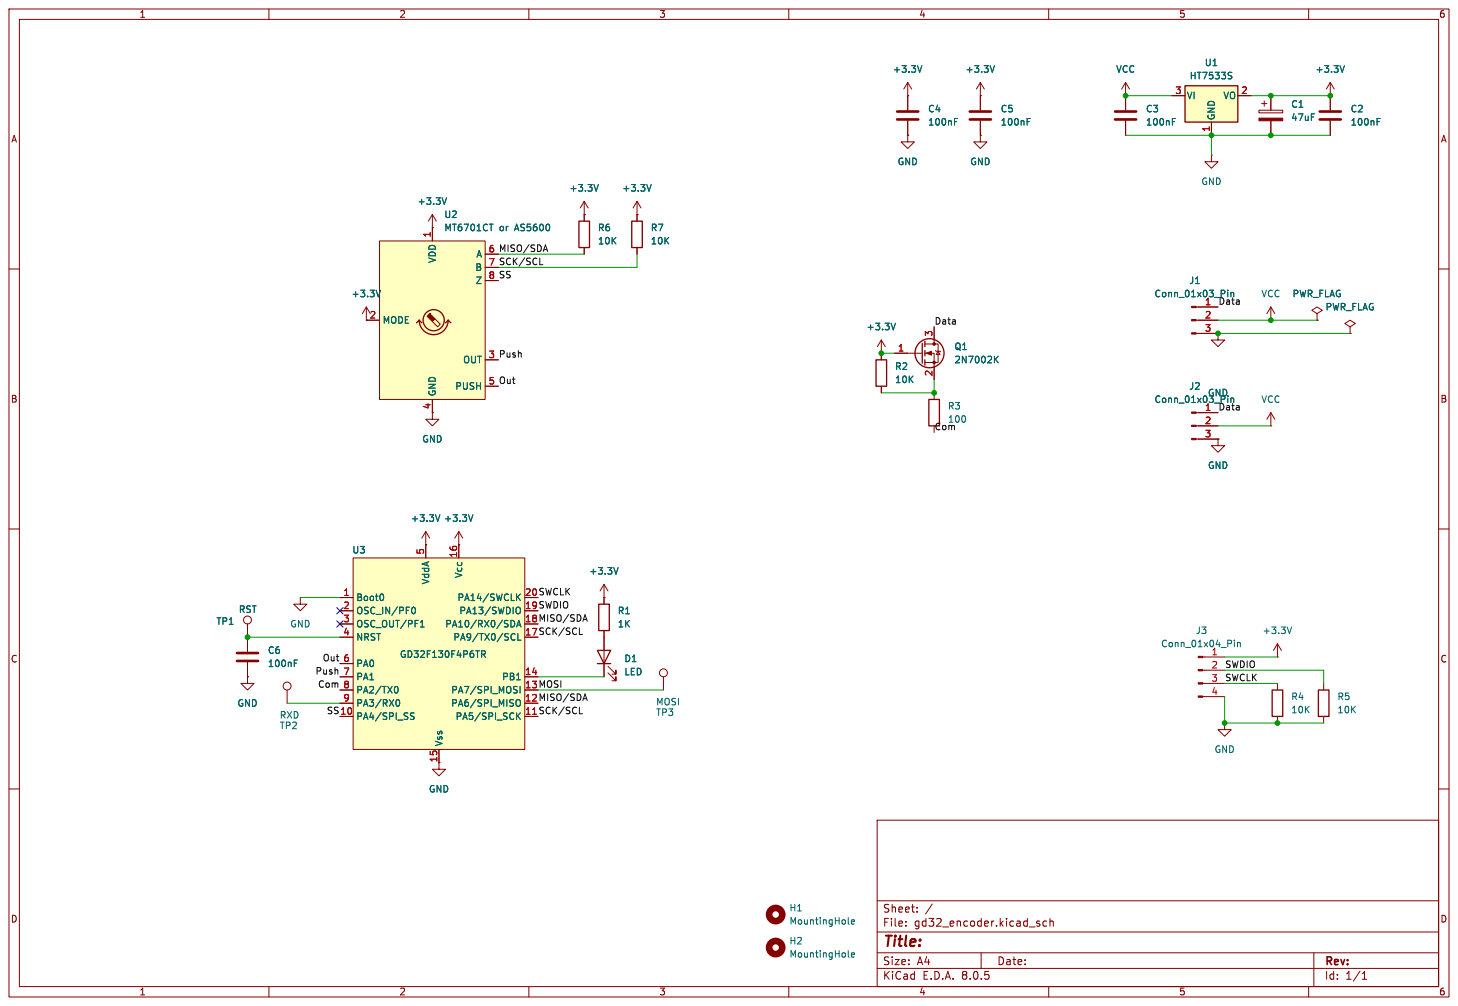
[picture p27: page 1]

1 VO 2 VI 3 +3.3V VCC GND GND

Data Data MISO/SDA

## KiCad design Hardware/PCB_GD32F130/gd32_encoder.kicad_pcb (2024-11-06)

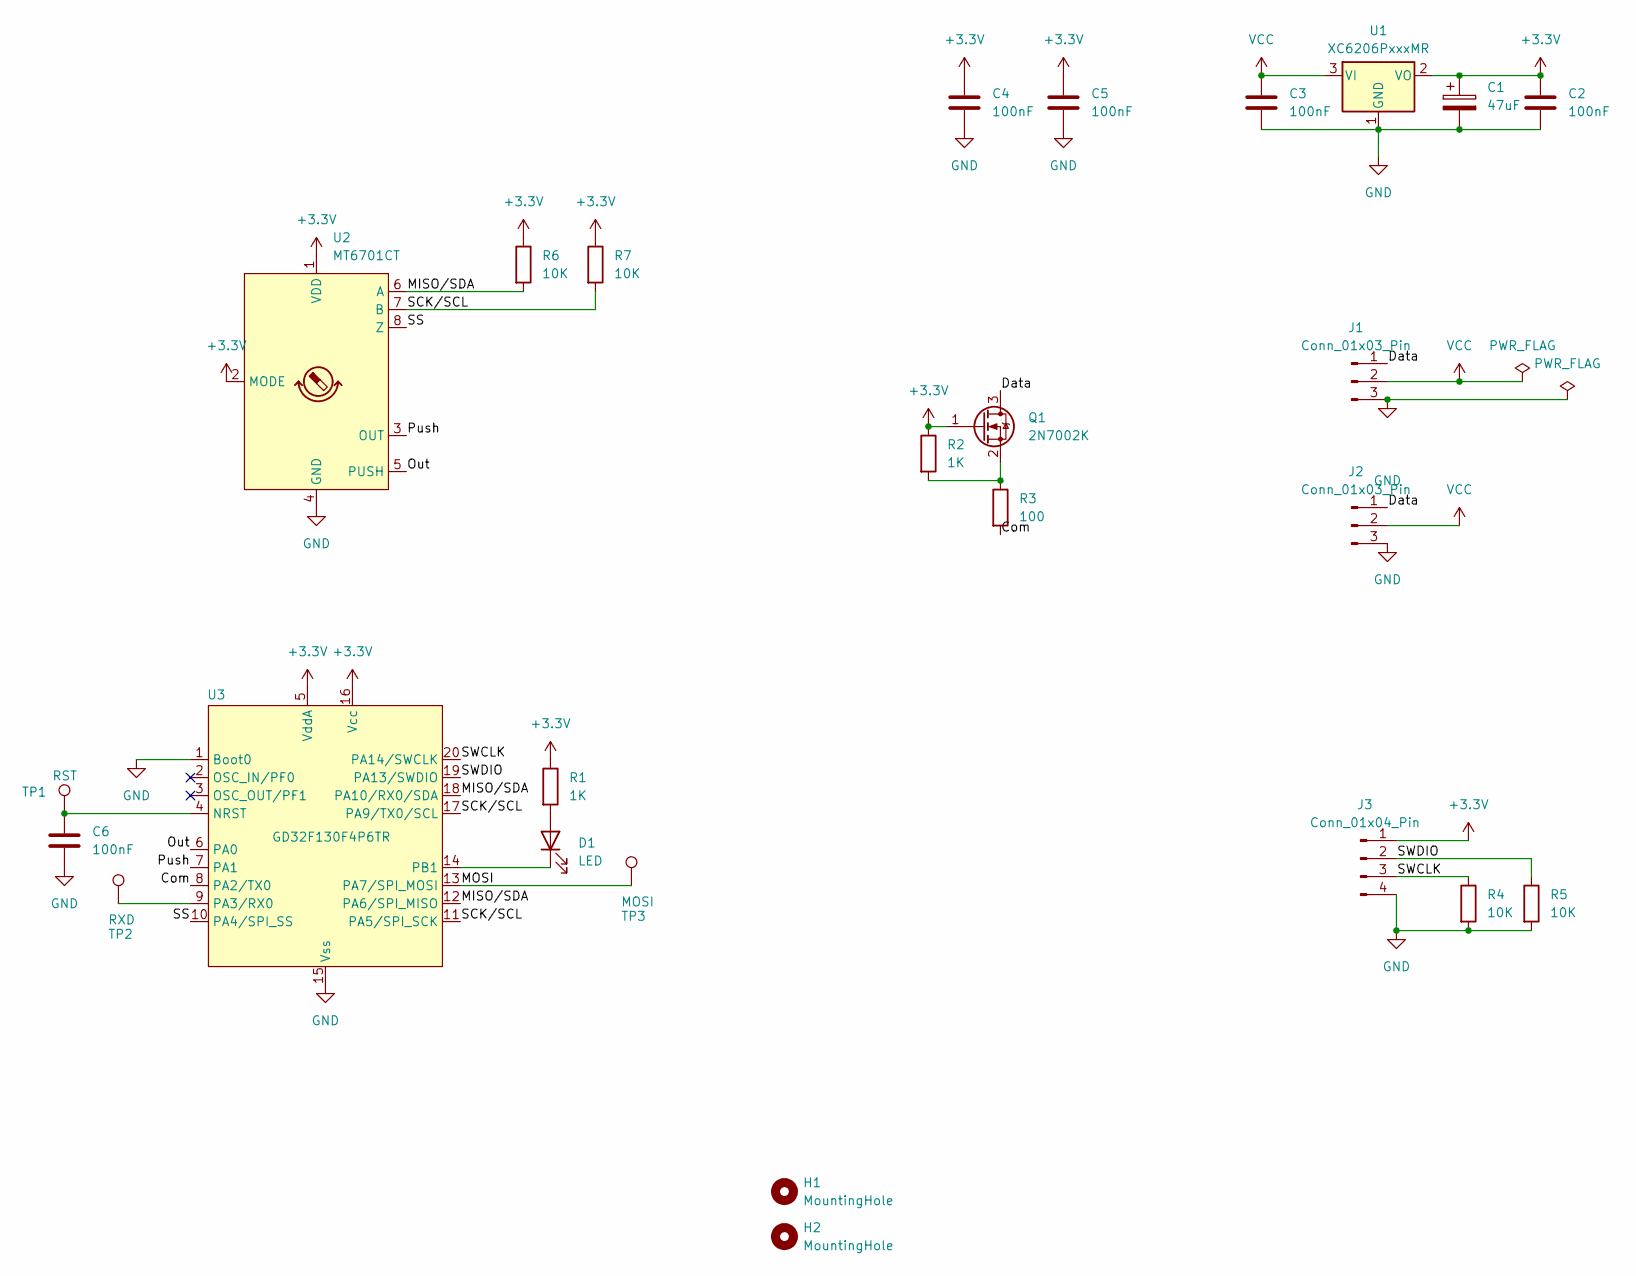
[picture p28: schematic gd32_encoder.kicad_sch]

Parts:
C1: 47uF; CP_EIA-3216-18_Kemet-A_Pad1.58x1.35mm_HandSolder
C2, C3, C4, C5, C6: 100nF; C_0603_1608Metric_Pad1.08x0.95mm_HandSolder
D1: LED; LED_0603_1608Metric_Pad1.05x0.95mm_HandSolder
H1, H2: MountingHole; MountingHole_2.2mm_M2_DIN965
J1, J2: Conn_01x03_Pin; JST_1x03_P2.50mm_Vertical
J3: Conn_01x04_Pin; PinHeader_1x04_P2.54mm_Vertical
Q1: 2N7002K; SOT-23
R1, R2: 1K; R_0603_1608Metric_Pad0.98x0.95mm_HandSolder
R3: 100; R_0603_1608Metric_Pad0.98x0.95mm_HandSolder
R4, R5, R6, R7: 10K; R_0603_1608Metric_Pad0.98x0.95mm_HandSolder
TP1: RST; PinHeader_1x01_P2.54mm_Vertical
TP2: RXD; TestPoint_Pad_D1.0mm
TP3: MOSI; TestPoint_Pad_D1.0mm
U1: XC6206PxxxMR; SOT-23-3
U2: MT6701CT; SO-8_3.9x4.9mm_P1.27mm
U3: GD32F130F4P6TR; TSSOP-20_4.4x6.5mm_P0.65mm

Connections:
+3.3V: C1.1, C2.1, C4.1, C5.1, J3.1, Q1.1 (G), R1.1, R2.1, R6.1, R7.1, U1.2 (VO), U2.1 (VDD), U2.2 (MODE), U3.5 (VddA), U3.16 (Vcc)
/Com: R3.2, U3.8 (PA2/TX0)
/Data: J1.1, J2.1, Q1.3 (D)
/MISO/SDA: R6.2, U2.6 (A), U3.12 (PA6/SPI_MISO), U3.18 (PA10/RX0/SDA)
/MOSI: TP3.1, U3.13 (PA7/SPI_MOSI); also elsewhere on the board
/Out: U2.5 (PUSH), U3.6 (PA0)
/Push: U2.3 (OUT), U3.7 (PA1)
/SCK/SCL: R7.2, U2.7 (B), U3.11 (PA5/SPI_SCK), U3.17 (PA9/TX0/SCL)
/SS: U2.8 (Z), U3.10 (PA4/SPI_SS)
/SWCLK: J3.3, R4.1, U3.20 (PA14/SWCLK)
/SWDIO: J3.2, R5.1, U3.19 (PA13/SWDIO)
GND: C1.2, C2.2, C3.2, C4.2, C5.2, C6.2, J1.3, J2.3, J3.4, R4.2, R5.2, U1.1 (GND), U2.4 (GND), U3.1 (Boot0), U3.15 (Vss)
unnamed: D1.2 (A), R1.2
unnamed: D1.1 (K), U3.14 (PB1)
unnamed: Q1.2 (S), R2.2, R3.1
unnamed: C6.1, TP1.1, U3.4 (NRST)
unnamed 16: TP2.1, U3.9 (PA3/RX0); also elsewhere on the board
VCC: C3.1, J1.2, J2.2, U1.3 (VI)

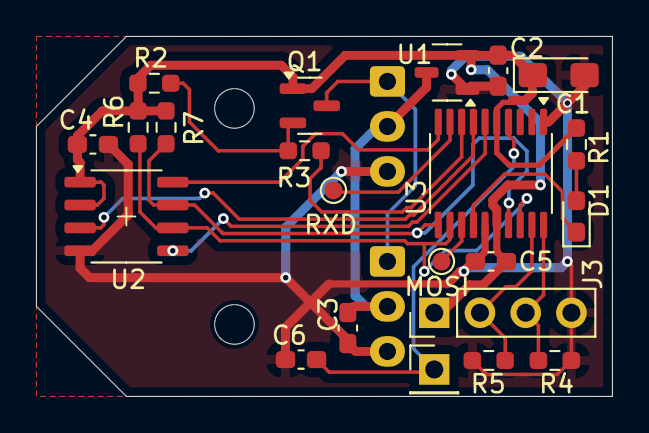
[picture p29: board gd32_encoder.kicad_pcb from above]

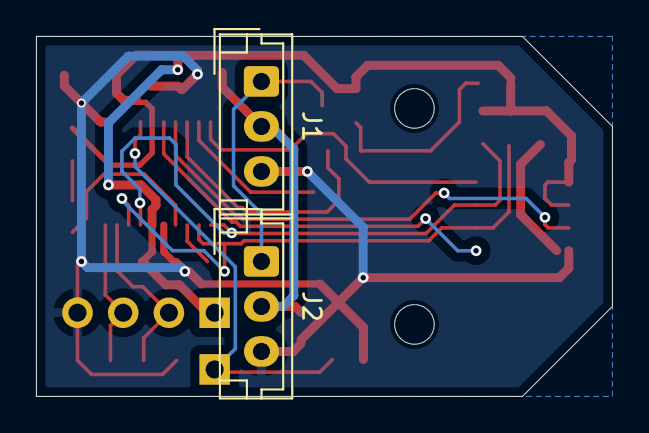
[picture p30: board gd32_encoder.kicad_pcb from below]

Board: 2 copper layers, 32.0 x 20.0 mm, 26 parts (2 on the bottom side), 18 nets.

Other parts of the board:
MOSI: MOSI; TestPoint_Pad_D1.0mm
RXD: RXD; TestPoint_Pad_D1.0mm

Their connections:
/MOSI: MOSI.1; also elsewhere on the board
unnamed 16: RXD.1; also elsewhere on the board

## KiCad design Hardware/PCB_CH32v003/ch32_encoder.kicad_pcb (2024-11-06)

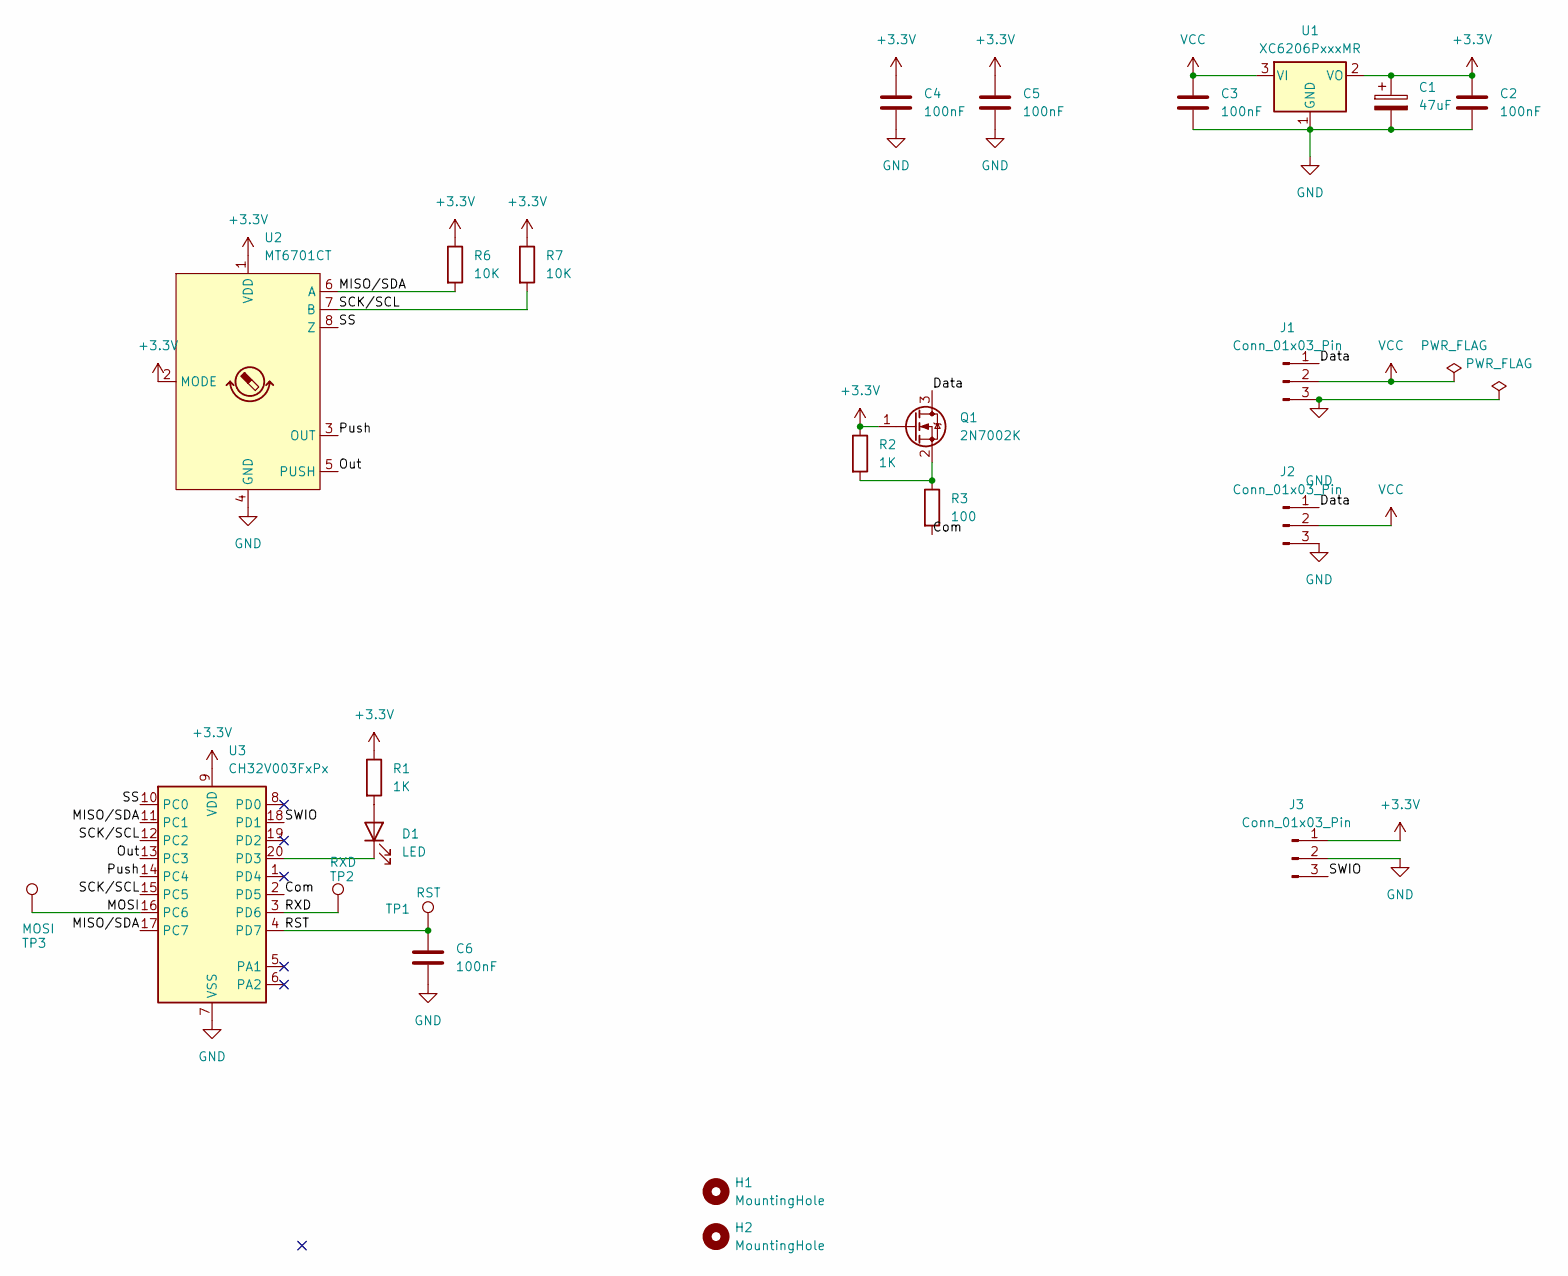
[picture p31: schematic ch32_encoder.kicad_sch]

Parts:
C1: 47uF; CP_EIA-3216-18_Kemet-A_Pad1.58x1.35mm_HandSolder
C2, C3, C4, C5, C6: 100nF; C_0603_1608Metric_Pad1.08x0.95mm_HandSolder
D1: LED; LED_0603_1608Metric_Pad1.05x0.95mm_HandSolder
H1, H2: MountingHole; MountingHole_2.2mm_M2_DIN965
J1, J2: Conn_01x03_Pin; JST_1x03_P2.50mm_Vertical
J3: Conn_01x03_Pin; PinHeader_1x03_P2.54mm_Vertical
Q1: 2N7002K; SOT-23
R1, R2: 1K; R_0603_1608Metric_Pad0.98x0.95mm_HandSolder
R3: 100; R_0603_1608Metric_Pad0.98x0.95mm_HandSolder
R6, R7: 10K; R_0603_1608Metric_Pad0.98x0.95mm_HandSolder
TP1: RST; PinHeader_1x01_P2.54mm_Vertical
TP2: RXD; TestPoint_Pad_D1.0mm
TP3: MOSI; TestPoint_Pad_D1.0mm
U1: XC6206PxxxMR; SOT-23-3
U2: MT6701CT; SO-8_3.9x4.9mm_P1.27mm
U3: CH32V003FxPx; TSSOP-20_4.4x6.5mm_P0.65mm

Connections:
+3.3V: C1.1, C2.1, C4.1, C5.1, J3.1, Q1.1 (G), R1.1, R2.1, R6.1, R7.1, U1.2 (VO), U2.1 (VDD), U2.2 (MODE), U3.9 (VDD)
/Com: R3.2, U3.2 (PD5)
/Data: J1.1, J2.1, Q1.3 (D)
/MISO/SDA: R6.2, U2.6 (A), U3.11 (PC1), U3.17 (PC7)
/MOSI: TP3.1, U3.16 (PC6); also elsewhere on the board
/Out: U2.5 (PUSH), U3.13 (PC3)
/Push: U2.3 (OUT), U3.14 (PC4)
/RST: C6.1, TP1.1, U3.4 (PD7)
/RXD: TP2.1, U3.3 (PD6); also elsewhere on the board
/SCK/SCL: R7.2, U2.7 (B), U3.12 (PC2), U3.15 (PC5)
/SS: U2.8 (Z), U3.10 (PC0)
/SWIO: J3.3, U3.18 (PD1)
GND: C1.2, C2.2, C3.2, C4.2, C5.2, C6.2, J1.3, J2.3, J3.2, U1.1 (GND), U2.4 (GND), U3.7 (VSS)
unnamed: D1.2 (A), R1.2
unnamed: D1.1 (K), U3.20 (PD3)
unnamed: Q1.2 (S), R2.2, R3.1
VCC: C3.1, J1.2, J2.2, U1.3 (VI)

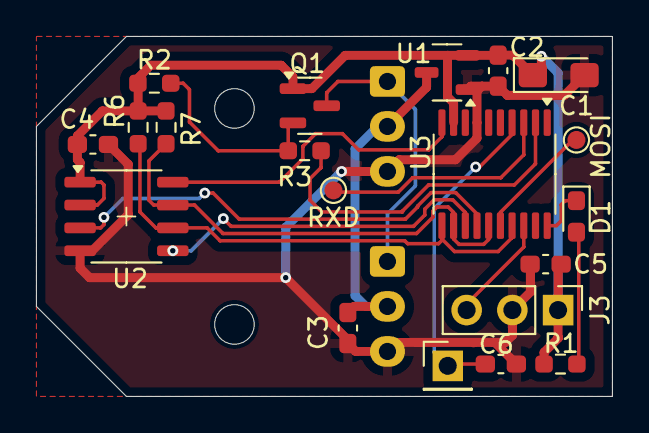
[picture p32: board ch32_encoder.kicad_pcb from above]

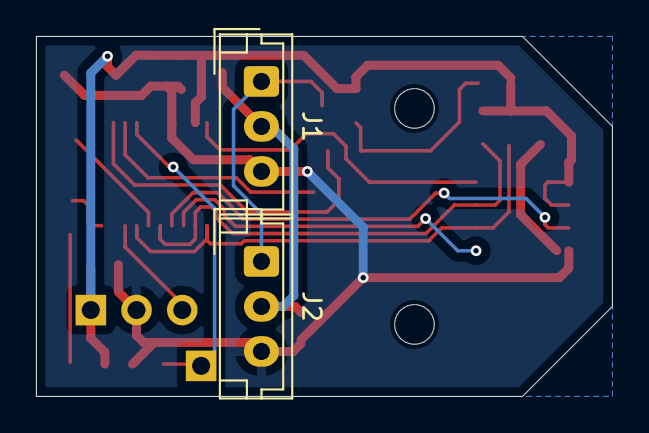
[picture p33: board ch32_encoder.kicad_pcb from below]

Board: 2 copper layers, 32.0 x 20.0 mm, 24 parts (2 on the bottom side), 17 nets.

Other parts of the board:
MOSI: MOSI; TestPoint_Pad_D1.0mm
RXD: RXD; TestPoint_Pad_D1.0mm

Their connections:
/MOSI: MOSI.1; also elsewhere on the board
/RXD: RXD.1; also elsewhere on the board

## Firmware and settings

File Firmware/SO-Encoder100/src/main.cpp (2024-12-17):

/*
https://emanual.robotis.com/docs/en/dxl/protocol1/
https://www.theremino.com/wp-content/uploads/files/SmartMotors/Feetech_Motors_Programming_ENG.pdf

FeeTech Documentation:
https://www.feetechrc.com/letter-of-agreement.html
https://www.feetechrc.com/Data/feetechrc/upload/file/20240702/%E8%88%B5%E6%9C%BA%E5%8D%8F%E8%AE%AE%E6%89%8B%E5%86%8C-%E7%A3%81%E7%BC%96%E7%A0%81%E7%89%88%E6%9C%AC.pd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

https://download.kamami.pl/p1181056-ST3215_Servo_User_Manual.pdf
https://www.waveshare.com/w/upload/f/f4/ST3215_Servo_User_Manual.pdf
https://www.waveshare.com/wiki/ST3215_Servo


GD32F130FxP6
  Datasheet: https://www.gigadevice.com.cn/Public/Uploads/uploadfile/files/20241008/GD32F130xxDatasheetRev4.0.pdf
  Manual: https://www.gigadevice.com.cn/Public/Uploads/uploadfile/files/20240407/GD32F1x0_User_Manual_Rev3.8.pdf

  GD32F130F4: UART0 (SERIAL1) TX: PA2, RX: PA3
  GD32F130F8: UART1 (SERIAL2) TX: PA2, RX: PA3

Scan:
999: FF FF FD 04 02 00 09 F3
 33: FF FF 00 04 02 00 09 F0
 29: 00 03 00 00 00 04 45 D8
 31: FF FF 01 04 02 00 09 EF 
   FF FF 01 0B 00 03 09 00 09 03 01 00 00 01 D9 FF FF 02 04 02 00 09 EE
 27: 02 03 00 00 00 04 44 3A
 32: FF FF 03 04 02 00 09 ED

Monitor:
 47: FF FF 01 04 02 38 11 AF FF FF 01 13 00 FC 07 00 00 28 04 45 19 00 00 00 00 08 00 00 00 00 56
 47: FF FF 01 04 02 38 11 AF FF FF 01 13 00 FC 07 00 00 28 04 45 19 00 00 00 00 08 01 00 00 00 55


 STS3215 Position Offset Experiments
======================================
// Position 1310 , Offset 300 => 1010
// Position 1310 , Offset -300 => 1010  !! UI Bug with bit 11 as sign??
// Position 1310 , Offset 300 + 2048 => UI Error: cannot set more than 2048 (UI bug?)
// Position 1311 , Torque Switch 128 => Offset: 2785 (2785 is -737) => 2048 (This value cannot be set from UI)
// Position 2502 , Torque Switch 128 => Offset: 454 => 2048
// Position limits are ignored when moving the motor manually. No negative positions. Wrap at 4095.
*/

#include <Arduino.h>

#include "Config.h"
#ifdef GD32F1
// Somehow EEPROM.h does not find this if not included first.
#include <FlashStorage.h>
#endif
#include <EEPROM.h>

// #include <SPI.h>
// #include "MT6701.h"

#include "i2c.h"
#include "AS5600_NB.h"

#define DXL_BROADCAST_ID 0xFE

#define DXL_PING_CMD 0x01
#define DXL_READ_CMD 0x02
#define DXL_WRITE_CMD 0x03
#define DXL_REG_WRITE_CMD 0x04
#define DXL_ACTION_CMD 0x05
#define DXL_FACTORY_RESET_CMD 0x06
#define DXL_REBOOT_CMD 0x08
#define DXL_SYNC_READ_CMD 0x82
#define DXL_SYNC_WRITE_CMD 0x83
#define DXL_BULK_READ_CMD 0x92


PROGMEM const char EMPTY_STRING[] =  "";
PROGMEM const char NEW_LINE[] =  "\n";

PROGMEM const char PROJECT_NAME[] = __PROJECT_NAME__;
PROGMEM const char PROJECT_VERSION[] = __PROJECT_VERSION__;
PROGMEM const char COMPILE_DATE[] = __DATE__;
PROGMEM const char COMPILE_TIME[] = __TIME__;

PROGMEM const servo_reg_t default_data = {
  3,     // firmware_major
  9,     // firmware_minor
  0,     // res1
  9,     // servo_minor
  3,     // servo_major
  DEFAULT_ID,     // id
  0,     // baudrate
  0,     // return_delay
  1,     // status_level
  0,     // min_angle
  4096,  // max_angle
  70,    // max_temp
  140,   // max_voltage
  30,    // min_voltage
  1000,  // max_torque
  12,    // phase_1
  44,    // unloading_cond
  47,    // led_alarm_cond
  0,     // position_pid_p
  0,     // position_pid_d
  0,     // position_pid_i
  0,     // max_start_force
  0,     // cw_sensitive_zone
  0,     // cc_sensitive_zone
  310,   // protection_current
  1,     // angle_resolution
  0,     // position_correction
  0,     // operation_mode
  20,    // protection_torque
  200,   // protection_time
  80,    // overload_torque
  0,     // speed_pid_p
  0,     // over_current_time
  0,     // velocity_pid_i
  0,     // torque_switch
  0,     // acceleration
  0,     // target_location
  0,     // operation_time
  0,     // operation_speed
  0,     // torque_limit
  0,     // res2
  0,     // res3
  0,     // res4
  1,     // lock_flag
  2048,  // current_location
  0,     // current_speed
  0,     // current_load
  33,    // current_voltage
  24,    // current_temp
  0,     // async_write_flag
  0,     // servo_status
  0,     // move_flag
  0,     // res5
  0,     // res6
  0,     // current_current
  0,     // res7
};

#if SERIAL_DEBUG
Print* debugStream = &LOGGER;
#endif

eeprom_data_t eeprom_data = {0};

servo_reg_t& reg = eeprom_data.registers.reg;
uint8_t* const reg_data = eeprom_data.registers.data;

uint8_t error = 0;

uint8_t rx_buffer[256];
uint8_t rx_index = 0;
uint32_t last_rx_ts = 0;
uint8_t ignore = 0;  // Ignore this many RX bytes. (What we just sent out.)

uint8_t sb_read_after_id = 0;
uint8_t sb_read_addr = 0;
uint8_t sb_read_len = 0;
uint32_t sb_read_timeout = 0;

// MT6701 mt6701;

I2C i2c0(0, SDA, SCL, 1000000);
AS5600_NB as5600(i2c0, AS5600_DIR_PIN);  

int16_t angle = 0;
int16_t old_angle = 0;
int32_t rotations = 0;
int32_t position = 0;
uint32_t last_data_ts = 0;

void debug_hex(const uint8_t* data, uint16_t len) {
  for (int i = 0; i < len; i++) {
    DEBUG_print(data[i], HEX);
    DEBUG_print(FST(" "));
  }
}


/***********************************************************\
 * Save Registers to EEPROM
\***********************************************************/
void save_eeprom() {
  eeprom_data.magic = EEPROM_MAGIC;
#ifdef GD32F1
#ifndef ARDUINO_GENERIC_F130F4PX
  EEPROM.begin();
  EEPROM.put(0, eeprom_data);
  EEPROM.commit();
#endif
#endif
#ifdef ESP32
  EEPROM.begin(EEPROM_SIZE);
  EEPROM.writeBytes(0, &eeprom_data, EEPROM_SIZE);
  EEPROM.commit();
  EEPROM.end();
#endif

  DEBUG_println(FST("# Saved data to EEPROM"));
}


/***********************************************************\
 * Ping
\***********************************************************/
void ping_cmd() {
  uint8_t header[] = {0xFF, 0xFF, reg.id, 2, error};

  // Calculate the CRC.
  uint8_t crc = 0;
  for (int i = PACKET_ID; i < sizeof(header); i++) {crc += header[i]; }
  crc = ~crc; // Invert the bits.

#ifdef COM
  // Send the response.
  COM.write(header, sizeof(header));
  COM.write(crc);
  ignore = sizeof(header) + 1;
#endif

#if SERIAL_DEBUG and 0
  debug_hex(header, sizeof(header));
  debug_hex(reg_data+addr, len);
  DEBUG_printf(FST("%02X\n"), crc);
#endif
}



/***********************************************************\
 * Write to registers
\***********************************************************/
void write_cmd(uint8_t addr, uint8_t len, const uint8_t* data) {
  uint8_t header[] = {0xFF, 0xFF, reg.id, 2, error};

  // Save the data to the registers.
  for (size_t i = 0; i < len; i++) {
    if (addr + i == 40 && data[i] == 128) {
      // Set Center Position
      int16_t pc = angle -2048;
      if (pc < 0) { pc = -pc; pc |= 0x800; }
      reg.position_correction = pc;
      rotations = 0;
    } else {
        reg_data[addr+i] = data[i];
    }
  }

  // Calculate the CRC.
  uint8_t crc = 0;
  for (int i = PACKET_ID; i < sizeof(header); i++) {crc += header[i]; }
  crc = ~crc; // Invert the bits.

  // Send the response.
#ifdef COM
  COM.write(header, sizeof(header));
  COM.write(crc);
#endif
  ignore = sizeof(header) + 1;

#if SERIAL_DEBUG
  debug_hex(data, len);
  DEBUG_print(FST(" => "));
  debug_hex(header, sizeof(header));
  DEBUG_println(crc, HEX);
#endif

}

/***********************************************************\
 * Read from registers
\***********************************************************/
void read_cmd(uint8_t addr, uint8_t len) {
  uint8_t header[] = {0xFF, 0xFF, reg.id, (uint8_t)(len + 2), error};

  // Calculate the CRC.
  uint8_t crc = 0;
  for (int i = PACKET_ID; i < sizeof(header); i++) {crc += header[i]; }
  for (int i = addr; i < addr+len; i++) {crc += reg_data[i]; }
  crc = ~crc; // Invert the bits.

#ifdef COM
  // Send the response.
  COM.write(header, sizeof(header));
  COM.write(reg_data+addr, len);
  COM.write(crc);
  ignore = sizeof(header) + len + 1;
#endif

#if SERIAL_DEBUG and 0
  debug_hex(header, sizeof(header));
  debug_hex(reg_data+addr, len);
  DEBUG_printf(FST("%02X\n"), crc);
#endif
}


/***********************************************************\
 * Sync Read from registers
\***********************************************************/
// TODO: Buffer data so that data from all servos is read at the exact same time?
void sync_read_cmd(uint8_t* packet) {
  uint8_t n = rx_buffer[PACKET_LENGTH] - 4;
  uint8_t* ptr = packet + 7;

  // Check if own ID is first.
  if (ptr[0] == reg.id) {
    DEBUG_println(FST("# Sync Read: Own ID is first."));
    return read_cmd(rx_buffer[PACKET_ADDR], rx_buffer[PACKET_LEN]);
  }

  // Check if own ID is in the rest of the list.
  uint8_t after_id = ptr[0];
  for (uint8_t i = 1; i < n; i++) {
    if (ptr[i] == reg.id) {
      // Wait until after servo with ID after_id responds.
      sb_read_after_id = after_id;
      sb_read_addr = rx_buffer[PACKET_ADDR];
      sb_read_len = rx_buffer[PACKET_LEN];
      sb_read_timeout = millis() + 1000;
      DEBUG_print(FST("# Sync Read: Own ID after: "));
      DEBUG_println(after_id);
      return;
    }
    after_id = ptr[i];
  }
}


/***********************************************************\
 * Bulk Read from registers
\***********************************************************/
void bulk_read_cmd(uint8_t* packet) {
  uint8_t n = rx_buffer[PACKET_LENGTH] - 3;
  uint8_t* ptr = packet + 6;

  // Check if own ID is first.
  if (ptr[1] == reg.id) {
    DEBUG_println(FST("# Bulk Read: Own ID is first."));
    return read_cmd(ptr[2], ptr[0]);
  }

  // Check if own ID is in the rest of the list.
  uint8_t after_id = ptr[1];
  for (uint8_t i = 3; i < n; i+=3) {
    if (ptr[i+1] == reg.id) {
      // Wait until after servo with ID after_id responds.
      sb_read_after_id = after_id;
      sb_read_addr = ptr[i+2];
      sb_read_len = ptr[i];
      sb_read_timeout = millis() + 1000;
      DEBUG_print(FST("# Bulk Read: Own ID after: "));
      DEBUG_println(after_id);
      return;
    }
    after_id = ptr[i+1];
  }

  DEBUG_println(FST("# Bulk Read: Own ID not found."));
}

/***********************************************************\
 * Execute a command
\***********************************************************/
void execute_command() {
  uint8_t instruction = rx_buffer[PACKET_INSTRUCTION];
  switch(instruction) {
    case DXL_PING_CMD: // Ping
      DEBUG_print(FST("# Ping\n"));
      ping_cmd();
      break;

    case DXL_READ_CMD: // Read
      {
        uint8_t addr = rx_buffer[PACKET_ADDR]; 
        uint8_t len = rx_buffer[PACKET_LEN];
        // DEBUG_printf(FST("# Read Adr:%d Len:%d => "), addr, len);
        read_cmd(addr, len);
      }
      break;

    case DXL_WRITE_CMD: // Write
      {
        uint8_t addr = rx_buffer[PACKET_ADDR]; 
        uint8_t len = rx_buffer[PACKET_LENGTH]-3;
        DEBUG_print(FST("# Write Adr:"));
        DEBUG_print(addr);
        DEBUG_print(FST("Len:"));
        DEBUG_println(len);
        bool save = false;
        if (addr == 55 && rx_buffer[PACKET_DATA] == 1 && reg.lock_flag == 0) { save = true; }
        write_cmd(addr, len, rx_buffer + PACKET_DATA);
        if (save) {save_eeprom();}
      }
      break;

    case DXL_REG_WRITE_CMD: // Reg Write
      DEBUG_print(FST("# Reg Write\n"));
      break;

    case DXL_ACTION_CMD: // Action
      DEBUG_print(FST("# Action\n"));
      break;

    case DXL_FACTORY_RESET_CMD: // Factory Reset
      DEBUG_print(FST("# Factory Reset\n"));
      break;

    case DXL_REBOOT_CMD: // Reboot
      DEBUG_print(FST("# Reboot\n"));
      ping_cmd();
#ifdef COM
      COM.flush();
      delay(42);
#endif
      { int a = 0; int b = 42 / a; }  // Crash
      break;

    case DXL_SYNC_READ_CMD: // Sync Read
      DEBUG_print(FST("# Sync Read\n"));
      sync_read_cmd(rx_buffer);
      break;

    case DXL_SYNC_WRITE_CMD: // Sync Write
      DEBUG_print(FST("# Sync Write\n"));
      break;

    case DXL_BULK_READ_CMD: // Bulk Read
      DEBUG_print(FST("# Bulk Read\n"));
      bulk_read_cmd(rx_buffer);
      break;

    default:  
      DEBUG_print(FST("# Unknown instruction: "));
      DEBUG_println(instruction);
      break;
  }
}

/***********************************************************\
 * Parse received data and wait for valid commands
\***********************************************************/
void parse_rx_data(uint8_t c) {
  // Ignore any bytes we sent ourselves.
  if (ignore) {
    ignore--;
    return;
  } 

  // Check for start of packet.
  if (rx_index == 0 && c != 0xFF) {
    return;
  }
  if (rx_index == 1 && c != 0xFF) {
    rx_index = 0;
    return;
  }
  rx_buffer[rx_index++] = c;
  last_rx_ts = millis();

  if (rx_index > 5 && rx_buffer[PACKET_LENGTH]+4 == rx_index) { // Full packet received.
    rx_index = 0;
    if(rx_buffer[PACKET_ID] != reg.id 
        && rx_buffer[PACKET_ID] != DXL_BROADCAST_ID 
        && sb_read_after_id == 0) { 
      // DEBUG_printf(FST("\n# Wrong ID: %02X, Length: %02X, Instruction: %02X\n"), rx_buffer[PACKET_ID], rx_buffer[PACKET_LENGTH], rx_buffer[PACKET_INSTRUCTION]);
      return;
    }

    // Checksum calculation: Checksum = ~( ID + Length + Instruction + Parameter1 + … Parameter N )
    uint8_t crc = 0;
    for (int i = PACKET_ID; i < rx_buffer[PACKET_LENGTH]+3; i++) {
      crc += rx_buffer[i];
    }
    crc = ~crc; // Invert the bits.

    if (crc != rx_buffer[rx_buffer[PACKET_LENGTH]+3]) {
      DEBUG_print(FST("\n# Bad CRC:"));
      DEBUG_print(crc);
      DEBUG_print(FST(", received: ")); 
      DEBUG_println(rx_buffer[rx_buffer[PACKET_LENGTH]+3]);
      return;
    }

    if (rx_buffer[PACKET_ID] == DXL_BROADCAST_ID 
          && rx_buffer[PACKET_INSTRUCTION] != DXL_SYNC_READ_CMD 
          && rx_buffer[PACKET_INSTRUCTION] != DXL_BULK_READ_CMD) {
      DEBUG_print(FST("\n# Unsupported broadcast CMD: "));
      DEBUG_println(rx_buffer[PACKET_INSTRUCTION], HEX);
      return;
    }

    if (sb_read_after_id) {
      DEBUG_print(FST("\n# Sync/Bulk Read got response from ID: "));
      DEBUG_println(rx_buffer[PACKET_ID]);
      if (rx_buffer[PACKET_ID] == sb_read_after_id) {
        DEBUG_println(FST("\n# Sync/Bulk Read got response from After ID"));
        read_cmd(sb_read_addr, sb_read_len);
        sb_read_after_id = 0;
        sb_read_addr = 0;
        sb_read_len = 0;
        sb_read_timeout = 0;
      }
      return;
    }

    execute_command();
  }
}


/***********************************************************\
 * Initialization Code
\***********************************************************/

void setup() {
  pinMode(LED_PIN, OUTPUT);
  digitalWrite(LED_PIN, HIGH);  

#if SERIAL_DEBUG
  LOGGER.begin(SERIAL_SPEED);
  delay(100);
  DEBUG_println(FST("\n\n# " __PROJECT_NAME__  " " __PROJECT_VERSION__ " " __DATE__ " " __TIME__));
#endif

#ifdef ARDUINO_GENERIC_F130F4PX
    memcpy(&eeprom_data.registers, &default_data, sizeof(default_data));
#else

#ifdef GD32F1
  EEPROM.begin();
  EEPROM.get(0, eeprom_data);
#endif
#ifdef ESP32
  EEPROM.begin(EEPROM_SIZE);
  EEPROM.readBytes(0, &eeprom_data, EEPROM_SIZE);
  EEPROM.end();
#endif
  if (eeprom_data.magic == EEPROM_MAGIC) {
    DEBUG_print(FST("# Loaded EEPROM data. ID: "));
    DEBUG_println(reg.id);
  } else {
#if SERIAL_DEBUG
    DEBUG_print(FST("# Invalid EEPROM magic: "));
    DEBUG_print(eeprom_data.magic);
    DEBUG_println(FST(". Using default values."));
    // DEBUG_printf(FST("# Size %d %d => "), sizeof(eeprom_data), EEPROM_SIZE); 
    debug_hex((uint8_t*)&eeprom_data, sizeof(eeprom_data));
    DEBUG_println();
#endif
    memcpy(&eeprom_data.registers, &default_data, sizeof(default_data));
  }
#endif

#ifdef COM
#ifdef GD32F1
  COM.begin(COM_SPEED, SERIAL_8N1);
  usart_halfduplex_enable(COM_UART);
  usart_enable(COM_UART);
#endif
#ifdef ESP32
  COM.begin(COM_SPEED, SERIAL_8N1, COM_RXD, COM_TXD);
#endif
#endif

  i2c0.begin();
  as5600.begin();

  // if (!as5600.isConnected()) {
  //   i2c0.end();
  //   SPI.begin();
  //   mt6701.initializeSSI(MT6701_CS_PIN);
  // }

  DEBUG_println(FST("# Init complete\n"));
}


/***********************************************************\
 * Main Loop
\***********************************************************/

void loop() {
  static uint32_t rx_time = 0;
  static uint32_t s_time = 0;

  uint32_t now = millis();

#ifdef COM
  // Handle Dynamixel communication.
  int r = COM.read();
  while (r != -1) {
    uint8_t c = (uint8_t)r;
    // if (now - rx_time > 20) {
    //   DEBUG_println();
    //   DEBUG_printf(FST("%3d: "), now - rx_time);
    // } 
    // DEBUG_printf(FST("%02X "), c);
    parse_rx_data(c);
    rx_time = now;
    r = COM.read();
  }

  if(rx_index && (millis() - last_rx_ts) > 10) { // RX Timeout
    DEBUG_println(FST("# RX Timeout"));
    rx_index = 0;
  }

  if (sb_read_after_id && now > sb_read_timeout) {
    DEBUG_print(FST("# Sync/Bulk Read: Timeout. After ID: "));
    DEBUG_println(sb_read_after_id);
    sb_read_after_id = 0;
  }
#endif

  // Handle sensor
  i2c0.run(now);
  if (as5600.run(now)) {
    // New data available.
    last_data_ts = now;
    angle = as5600.getAngle();
    if (angle != old_angle) { 
      if (angle < 1024 &&  old_angle > 1024*3) {rotations++;}
      else if (angle > 1024 * 3 &&  old_angle < 1024) {rotations--;}
      old_angle = angle;
    }

    int pc = reg.position_correction & 0x07FF;
    if (reg.position_correction & 0x800) { pc = -pc; } // Bit 11 is the sign bit.

    position = (int32_t)((angle - pc) & 0x0FFF) + (rotations << 12);

    if (reg.max_angle == 0 && reg.min_angle == 0) {
      // Multi Rotations Enabled
      if (position < 0) {position = (-position) | 0x8000;}
    } else {
      position &= 0x0FFF;
      // if (position < reg.min_angle) {position = reg.min_angle;}
      // if (position > reg.max_angle) {position = reg.max_angle;}
    }
    reg.current_location = position;
  }

  static uint32_t ptime = 0;
  if (now > ptime) {
    digitalWrite(LED_PIN, !digitalRead(LED_PIN));
    ptime = now + 100; 
    if (!as5600.isConnected() || (now > last_data_ts+100) ) { ptime += 900; /* slow blink */}

#if SERIAL_DEBUG
    DEBUG_print(FST("Angle:"));
    DEBUG_print(as5600.getAngle());
    DEBUG_print(FST(" Rotations:"));
    DEBUG_print(as5600.getRotations());
    DEBUG_print(FST(" Position:"));
    DEBUG_print(as5600.getPosition());
    DEBUG_print(FST(" Servo:"));
    DEBUG_println(reg.current_location);
#endif
  } 
}

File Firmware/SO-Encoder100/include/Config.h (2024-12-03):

#pragma once

#include <Arduino.h>

/********************************************\
|* GD32 Pin Definitions
\********************************************/

#ifdef GD32F1
#define LED_PIN PB1
#define SPI_SS_PIN PA4


#ifdef ARDUINO_GENERIC_F130F8PX
// F8 uses different pins for Serial than F4. Use Serial 2 for PA2/PA3
#define COM Serial2
#define LOGGER Serial2
#define COM_UART UART_1
#elif ARDUINO_GENERIC_F130F4PX
#define COM Serial1
#define LOGGER Serial1
#define COM_UART UART_0
#else 
#define COM Serial
#endif

#define COM_TXD PA2
#define COM_RXD PA3  // Not used in half duplex mode

#define MT6701_CS_PIN PA4
#define AS5600_DIR_PIN PA4

#define SERIAL_DEBUG 0

#else

/********************************************\
|* ESP32 Pin Definitions
\********************************************/

/*
https://drive.google.com/file/d/1gbKM7DA7PI7s1-ne_VomcjOrb0bE2TPZ/view
---+------+----+-----+-----+-----------+---------------------------
No.| GPIO | IO | RTC | ADC | Default   | Function
---+------+----+-----+-----+-----------+---------------------------
25 |   0* | IO | R11 | 2_1 | Boot      | 
35 |   1  | IO |     |     | UART0_TXD | USB Programming/Debug
24 |   2* | IO | R12 | 2_2 |           | 
34 |   3  | IO |     |     | UART0_RXD | USB Programming/Debug
26 |   4* | IO | R10 | 2_0 |           | 
29 |   5* | IO |     |     | SPI0_SS   | LED
14 |  12* | IO | R15 | 2_5 |           | 
16 |  13  | IO | R14 | 2_4 |           | 
13 |  14  | IO | R16 | 2_6 |           | MT6701 CS / AS5600 DIR
23 |  15* | IO | R13 | 2_3 |           | 
27 |  16+ | IO |     |     | UART2_RXD | BUS_RXD
28 |  17+ | IO |     |     | UART2_TXD | BUS_TXD 
30 |  18  | IO |     |     | SPI0_SCK  | MT6701 SCK
31 |  19  | IO |     |     | SPI0_MISO | MT6701 MISO
33 |  21  | IO |     |     | I2C0_SDA  | AS5600 SDA
36 |  22  | IO |     |     | I2C0_SCL  | AS5600 SCL
37 |  23  | IO |     |     | SPI0_MOSI | 
10 |  25  | IO | R06 | 2_8 |DAC1/I2S-DT| 
11 |  26  | IO | R07 | 2_9 |DAC2/I2S-WS| 
12 |  27  | IO | R17 | 2_7 | I2S-BCK   | 
8  |  32  | IO | R09 | 1_4 |           | 
9  |  33  | IO | R08 | 1_5 |           | 
6  |  34  | I  | R04 | 1_6 |           | 
7  |  35  | I  | R05 | 1_7 |           | 
4  |  36  | I  | R00 | 1_0 | SENSOR_VP | 
5  |  39  | I  | R03 | 1_3 | SENSOR_VN | 
3  |  EN  | I  |     |     | RESET     | 
---+------+----+-----+-----+-----------+---------------------------
(IO6 to IO11 are used by the internal FLASH and are not useable)
22 x I/O  + 4 x input only = 26 usable pins 
GPIO_34 - GPIO_39 have no internal pullup / pulldown.
- ADC2 can not be used with WIFI/BT (easily)
+ GPIO 16 and 17 are not available on WROVER (PSRAM)
* Strapping pins: IO0, IO2, IO4, IO5 (HIGH), IO12 (LOW), IO15 (HIGH)
*/


#define BUTTON_PIN 0
#define LED_PIN 5

#define I2C_SDA_PIN 21
#define I2C_SCL_PIN 22

#define SPI_MOSI_PIN 23
#define SPI_SCK_PIN 18
#define SPI_MISO_PIN 19

#define MT6701_CS_PIN 14
#define AS5600_DIR_PIN 14

#define COM Serial2 
#define COM_TXD 16
#define COM_RXD 17

#define SERIAL_DEBUG 1
#define LOGGER Serial

#endif


// Programming and debug

/* ============================================== *\
 * Constants
\* ============================================== */

#define LOOP_DELAY 100

#define __PROJECT_NAME__ "SO-Encoder100"
#define __PROJECT_VERSION__ "0.2"

#define COM_SPEED 1000000

#define SERIAL_SPEED 115200

#define MT6701_ALTERNATE_ADDRESS 0x46

extern const char EMPTY_STRING[];
extern const char NEW_LINE[];

extern const char PROJECT_NAME[] PROGMEM;
extern const char PROJECT_VERSION[] PROGMEM;
extern const char COMPILE_DATE[] PROGMEM;
extern const char COMPILE_TIME[] PROGMEM;

#define FST (const char *)F
#define PM (const __FlashStringHelper *)


/* ============================================== *\
 * Servo Registers
\* ============================================== */

#define DEFAULT_ID 1
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

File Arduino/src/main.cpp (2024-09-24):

/*======================================================================*\
 * ESP32-S3 Magnetic Encoder Controller for SO-ARM100 Leader
\*======================================================================*/

/*
 * Read six MT6701 magnetic encoders over SSI (SPI) and send the data to the
 * UART serial port.
 * 
 * The MT6701 has a 14 bit resolution (0-16383).
 * To address six encoders, 10 wires are needed: VCC, GND, Clock, Data, 6 x CS.
 * 
 * https://www.lcsc.com/datasheet/lcsc_datasheet_2110291630_Magn-Tek-MT6701QT-STD_C2913974.pdf
 * 
 * Vcc is 3.3V or 5V, but EEPROM programming needs 5V. ESP32 I/O is not 5V tolerant.
 * 
 */


#include <Arduino.h>
#include "Config.h"
#include <SPI.h>
#include <EEPROM.h>
#include "MT6701.h"

PROGMEM const char EMPTY_STRING[] =  "";
PROGMEM const char NEW_LINE[] =  "\n";

PROGMEM const char PROJECT_NAME[] = __PROJECT_NAME__;
PROGMEM const char PROJECT_VERSION[] = __PROJECT_COMPILE__;
PROGMEM const char COMPILE_DATE[] = __DATE__;
PROGMEM const char COMPILE_TIME[] = __TIME__;

PROGMEM const int ENCODER_PIN[] = {SPI_CS0_PIN, SPI_CS1_PIN, SPI_CS2_PIN, SPI_CS3_PIN, SPI_CS4_PIN, SPI_CS5_PIN};


Print* debugStream = &LOGGER;

MT6701 encoder[ENCODER_COUNT];

typedef struct {
  float angle;
  mt6701_status_t status;
} encoder_data_t;

encoder_data_t data[ENCODER_COUNT] = {0};
float home_angle[ENCODER_COUNT] = {0};

#ifdef CONFIG_IDF_TARGET_ESP32S3
#define HAS_RGB_LED 1
#endif

/***********************************************************\
 * Initialization Code
\***********************************************************/

void setup() {
#ifdef HAS_RGB_LED
  // There is currently a bug in the ESP32-S3 neopixelWrite() code. This will produce the 
  // following errors and the RGB LED will not light up.:
  //  E (19) rmt: rmt_set_gpio(526): RMT GPIO ERROR
  //  E (19) rmt: rmt_config(686): set gpio for RMT driver failed
  //  ==> Remove the #ifdef RGB_BUILTIN logic in the neopixelWrite() code.
  neopixelWrite(RGB_BUILTIN, 0, 10, 10);
#else
  pinMode(LED_PIN, OUTPUT);
  digitalWrite(LED_PIN, HIGH);  
#endif

  pinMode(BUTTON_PIN, INPUT_PULLUP);

  LOGGER.begin(SERIAL_SPEED);
  delay(1000);
  DEBUG_printf(FST("\n\n# %s %s | %s | %s\n"), PROJECT_NAME, PROJECT_VERSION, COMPILE_DATE, COMPILE_TIME);

  EEPROM.begin(EEPROM_SIZE);
  eeprom_data_t eeprom_data;
  EEPROM.get(0, eeprom_data);
  if (eeprom_data.magic == EEPROM_MAGIC) {
    memcpy(home_angle, eeprom_data.home_angle, sizeof(home_angle));
    DEBUG_print(FST("# Home angles loaded from EEPROM: "));
    for (int i = 0; i < ENCODER_COUNT; i++) {
      DEBUG_printf(FST("%0.2f"), home_angle[i]);
      if (i < ENCODER_COUNT - 1) { DEBUG_print(FST(", ")); }
    }
    DEBUG_println();
#ifdef HAS_RGB_LED
    neopixelWrite(RGB_BUILTIN, 0, 10, 0);
#endif
  } else {
    DEBUG_println(FST("# No valid EEPROM data found"));
#ifdef HAS_RGB_LED
    neopixelWrite(RGB_BUILTIN, 10, 10, 0);
#endif
  }
  EEPROM.end();

  SPI.begin();
  for (int i = 0; i < ENCODER_COUNT; i++) {
    bool ok = encoder[i].initializeSSI(ENCODER_PIN[i]);
    DEBUG_printf(FST("# Init Encoder %d, CS pin %d: %d\n"), i, ENCODER_PIN[i], ok);
  }

  DEBUG_println(FST("# Init complete\n"));
}


/***********************************************************\
 * Main Loop
\***********************************************************/

void loop() {
  static bool last_button = HIGH;
  u32_t start = millis();

  // Read all encoders and check if the data has changed.
  bool change = false;
  for (int i = 0; i < ENCODER_COUNT; i++) {
    mt6701_status_t status = encoder[i].fieldStatusRead();
    float angle = encoder[i].angleRead();
    if (angle != data[i].angle || status != data[i].status) {
      change = true;
      data[i].angle = angle;
      data[i].status = status;
    }
  }

  // Save the home position if the button is pressed.
  bool button = digitalRead(BUTTON_PIN);
  if (button == LOW && last_button == HIGH) {
    for (int i = 0; i < ENCODER_COUNT; i++) {
      home_angle[i] = data[i].angle;
    }
    change = true;
    // Save calibration angles to EEPROM.
    EEPROM.begin(EEPROM_SIZE);
    eeprom_data_t eeprom_data;
    eeprom_data.magic = EEPROM_MAGIC;
    memcpy(eeprom_data.home_angle, home_angle, sizeof(home_angle));
    EEPROM.put(0, eeprom_data);
    EEPROM.end();
    DEBUG_println(FST("# Saved Home Position to EEPROM"));
  }
  last_button = button;

  // Output a record if there was a change.
  if (change || ALWAYS_SEND) {
    DEBUG_printf(FST("%d, "), start);
    for (int i = 0; i < ENCODER_COUNT; i++) {
      float angle = home_angle[i] - data[i].angle;
      if (angle < 0) { angle += 360.0; }
      if (angle > 180.0) { angle -= 360.0; }
      //if (angle < -360.0) { angle += 360.0; }
      //if (angle > 360.0) { angle -= 360.0; }
      DEBUG_printf(FST("%0.2f,%d"), angle , data[i].status);
      if (i < ENCODER_COUNT - 1) { DEBUG_print(FST(", ")); } 
    }

    DEBUG_println();
  }

  // Wait for the next loop.
  delay(LOOP_DELAY - (millis() % LOOP_DELAY));
}



#if 0
//========================= Old I2C code =========================
//========================= Old I2C code =========================
//========================= Old I2C code =========================

void setup() {
#ifdef CONFIG_IDF_TARGET_ESP32S3
  // There is currently a bug in the neopixelWrite() code. This will produce the 
  // following errors and the RGB LED will not light up.:
  //  E (19) rmt: rmt_set_gpio(526): RMT GPIO ERROR
  //  E (19) rmt: rmt_config(686): set gpio for RMT driver failed
  //  ==> Remove the #ifdef RGB_BUILTIN logic in the neopixelWrite() code.
  neopixelWrite(RGB_BUILTIN, 0, 0, 10);
#else
  pinMode(LED_PIN, OUTPUT);
  digitalWrite(LED_PIN, HIGH);  
#endif

  LOGGER.begin(SERIAL_SPEED);
  delay(1000);
  DEBUG_printf(FST("\n\n%s %s | %s | %s\n"), PROJECT_NAME, PROJECT_VERSION, COMPILE_DATE, COMPILE_TIME);

  Wire.begin(I2C_SDA1_PIN, I2C_SCL_PIN);
  encoder[0].initializeI2C();
  Wire.end();
  Wire.begin(I2C_SDA2_PIN, I2C_SCL_PIN);
  encoder[1].initializeI2C();
  //Wire.end();

}

void printEncoderData(MT6701& encoder){
  float angle = encoder.angleRead();
  mt6701_status_t status = encoder.fieldStatusRead();
  DEBUG_printf(FST("%0.2f, %d | "), angle, status);
}

void loop() {
  Wire.begin(I2C_SDA1_PIN, I2C_SCL_PIN);
  printEncoderData(encoder[0]);
  Wire.end();
  Wire.begin(I2C_SDA2_PIN, I2C_SCL_PIN);
  //delay(10);
  printEncoderData(encoder[1]);
  //delay(10);
  Wire.end();
  DEBUG_println();
  delay(100);
}

#endif

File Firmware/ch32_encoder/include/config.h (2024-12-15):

#pragma once

#define SWIO_PIN PD1 // Program / Debug

#define LED_PIN PD3
#define TXD_PIN PD5
#define RXD_PIN PD6

#define SDA_PIN PC1
#define SCL_PIN PC2

#define OUT_PIN PC3
#define PUSH_PIN PC4

#define SS_PIN PC0
#define SCK_PIN PC5
#define MOSI_PIN PC6
#define MISO_PIN PC7

#define DEBUG 1

//#define millis() (SysTick->CNT / DELAY_MS_TIME)

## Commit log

2024-10-04 added 3D models
    [Encoder Dummy Servo.3mf, Encoder Dummy Servo.f3d]
2024-10-05 big board
2024-10-13 track test added
2024-10-16 added custom PCB
    [encoder.kicad_pcb, encoder.kicad_sch]
2024-11-06 Added PCB for CH32V003, which is a bit cheaper. New revision of GD32F130 PCB.
    [ch32_encoder.kicad_pcb, ch32_encoder.kicad_sch, ch32_encoder_bom.csv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]
2024-11-13 Start of GD32130 Encoder firmware
2024-11-17 Implemented non blocking GD32F130 drivers for I2C and AS5600
2024-11-21 Added solder stencil, images, PCB 3d model and schematic PDF.
    [ch32_encoder_v0.7.step, gd32_encoder_v0.7.step]
2024-11-27 Work on documentation
    [Servo Custom PCB V1.f3d, Servo Custom PCB V2.3mf]
2024-12-03 Updated 3.3V regulator with HT7533S that supports 12V input. / Mentioned AS5600 compatibility.
    [ch32_encoder.kicad_sch, ch32_encoder_bom.csv, gd32_encoder.kicad_sch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]
2024-12-03 Disabled EEPROM for GD32F130F4. The EEPROM driver uses too much RAM for this device. Servo ID needs to be hard coded for now.
    [Config.h, main.cpp]
2024-12-04 Changed PCB height for more connector clearance. Added Fusion 360 file.
    [Servo Custom PCB V2.3mf, Servo Custom PCB V2.f3d]
2024-12-11 Reorganized 3D modles
    [Encoder Dummy Servo.3mf, Encoder Dummy Servo.f3d, Servo Custom PCB V1.3mf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]
2024-12-13 Fixes for V1 3D model
    [Servo Custom PCB V1.3mf, Servo Custom PCB V1.f3d]
2024-12-14 Added feature: Torque Switch = 128 => Set Center Position
2024-12-17 sync read bug fix
    [main.cpp]
2025-01-04 Fixed R2 resistor value
    [ch32_encoder.kicad_sch, ch32_encoder_bom.csv, gd32_encoder.kicad_sch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]
